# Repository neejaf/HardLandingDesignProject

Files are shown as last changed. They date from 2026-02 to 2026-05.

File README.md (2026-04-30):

# Hard Landing – Landing Gear Design Project

This repository contains all materials for the MEE 342 landing gear design project.

## Project Phases
- [Phase 1 – System Description and Kinematics](phase1.md)
- [Phase 2 – Detailed CAD Design and Engineering Analysis](phase2.md)
- [Phase 3 – Prototyping, Testing and Reflection](phase3.md)

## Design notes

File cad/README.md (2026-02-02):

# CAD

This directory contains CAD models and exported files for the landing gear design.

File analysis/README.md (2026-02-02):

# Analysis

This folder contains hand calculations, kinematic derivations, and summaries of simulation results.

Detailed analysis will be added in later phases.

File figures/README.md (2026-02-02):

# Figures

This folder contains sketches, diagrams, CAD screenshots, and images used in the project report.

Figures will be added as the design progresses.

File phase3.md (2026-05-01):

# Phase 3 – Prototyping, Testing & Reflection

## Fabrication Details

- Printer: Bambu Lab P1S  
- Material: PLA  
- Settings:  
  - Preset: 0.20 mm Standard (Bambu Studio)  
  - Supports: Tree supports  
- Scale:
  - Entire assembly scaled to 4.2% of original design  
  - Pins scaled further (ex: 60 mm → 50 mm → then scaled 4.2%)

- Reprints:
  - Wheels/Tires:
    - Originally hollow → poor print quality
    - Redesigned as solid → reprinted successfully

- Notes:
  - Supported regions had poor surface finish  
  - Small scale reduced print accuracy  

---

## Assembly Procedure

- Strut + torque link + pins printed as one piece  
- Bogie printed with pin pre-inserted (snap-fit into strut fork)  
- Wheels and tires printed together  
- Tires spray painted black  

---

## Assembly Challenges

- Tight tolerances did not scale well  
- Pins difficult to fit at small scale  
- Rough surfaces from supports affected fit  

---

## Testing Plan

- Checked:
  - Rotation of joints  
  - Fit between components  
  - General smoothness  

---

## Results

- Snap-fit worked for bogie connection  
- Rotation was functional but not perfectly smooth  
- Supported areas showed reduced quality  

---

## Comparison to Phase 2

- Expected:
  - Clean fits and smooth motion  
- Actual:
  - Tolerance issues and rough interfaces  
  - Reduced precision due to scaling  

---

## Failures & Mistakes

- Designed tolerances based on CAD, not printer capability  
- Scaling to 4.2% made tolerances too tight  
- Hollow wheel design failed → required redesign  
- Overuse of supports reduced surface quality  

### Link Failure (Retraction Link)

One of the critical failures occurred in the retraction link component (shown below).

<table>
  <tr>
    <td align="center">
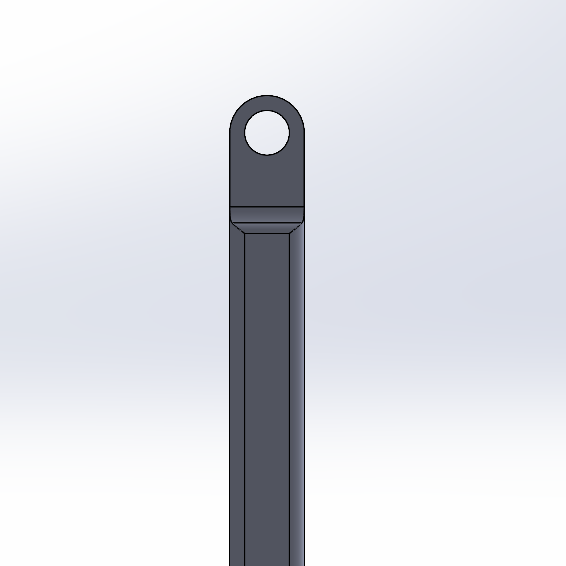
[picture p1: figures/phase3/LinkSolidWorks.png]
      <br>
      CAD Model
    </td>
    <td align="center">
      <br>
      Printed Part
    </td>
  </tr>
</table>

- In the CAD model, the hole regions had sufficient surrounding material for strength
- However, after scaling to 4.2% and printing in PLA:
  - The effective wall thickness around the holes was significantly reduced
  - Layer-based printing introduced weak points around the circular geometry
- This resulted in a stress concentration at the hole
- The part failed at this location during handling/assembly and required reprinting

Root Cause:
- Geometry was not adjusted for small-scale manufacturing
- Printer resolution limits reduced effective material thickness
- Layer adhesion + circular hole geometry weakened the region further

### Poor Surface Quality / Stringing (Strut Component)

<p align="center">
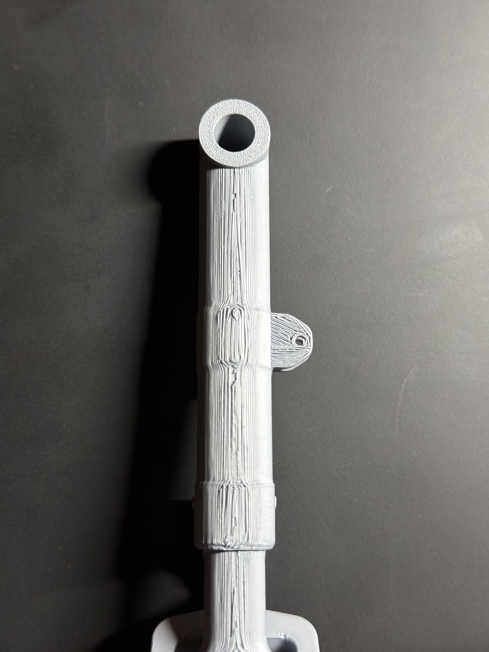
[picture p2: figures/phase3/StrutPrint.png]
  <br>
  Printed Strut (Surface Defects / Stringing)
</p>

The strut component exhibited noticeable surface defects and stringing, particularly along vertical faces.

- The print showed:
  - Stringing between features  
  - Uneven extrusion lines  
  - Rough surface finish  

- These defects were most prominent in:
  - Thin vertical sections  
  - Areas with frequent start/stop of extrusion  
  - Regions requiring support  

Root Cause:
- Small scale (4.2%) reduced feature resolution  
- Standard print settings were not optimized for fine features  
- Retraction and cooling were not ideal for this geometry  

Impact:
- Reduced surface quality  
- Potential reduction in strength  
- Poorer fit between components

## Improvements (Version 2)

- Increase tolerances for all mating parts  
- Reduce reliance on small pins  
- Design for fewer supports (better orientation)  
- Avoid hollow features at small scale  
- Consider larger scale or finer print settings  

---

## Key Takeaways from Design

- CAD tolerances ≠ printable tolerances  
- Scaling down amplifies manufacturing limitations  
- Supports negatively affect surface finish  

## Key Takeaways from Building

- Design for assembly tends to add extra complexity to model
- Proper engineering design process takes multiple physical models (as shown by our "Improvements" section)
- Orientation of 3D print greatly impacts strength of parts
- How to scale stress down from ANSYS to 3D model

<p align="center">
  <br>
  Final Model w/ Poster
</p>

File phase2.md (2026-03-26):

# Phase Two: Project Report  
Hard Landing – Landing Gear Project  

<p align="center">
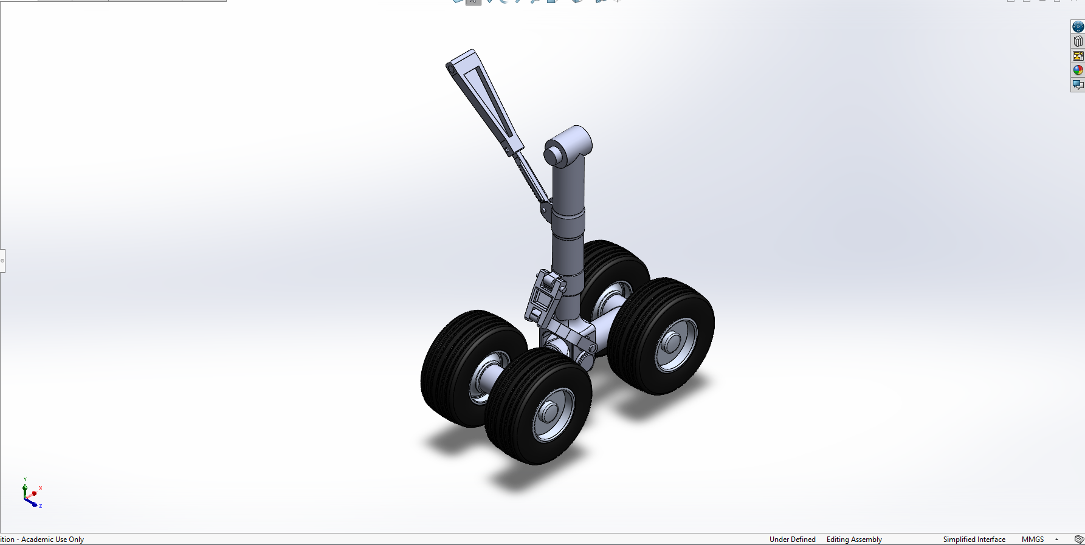
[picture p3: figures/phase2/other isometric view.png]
    </td>
  <p/>

<p align="center">
Aiden Beam, Jack Bessette, Ben Kolecki, Evan Morris, Nordin Jafar 
<p align="center">
Arizona State University
  </p>
<p align="center">
MEE 342  
  </p>

## **Final Design Overview**
This landing gear system is designed for a wide-body commercial aircraft operating under typical taxi, takeoff, landing, and flight conditions. During ground operation, the gear remains in its vertical, locked configuration to support the aircraft, and retracts during flight to reduce aerodynamic drag.

The design is based on a representative aircraft weight consisting of structural mass and payload. For loading assumptions, 90% of the total aircraft weight was taken to be supported by the main landing gear, with the remaining load carried by the nose gear. Since there are two main landing gear assemblies, each gear supports approximately 45% of the total aircraft weight under static conditions.

The system consists of three primary sections:
- **Main strut and wheel assembly**, which carries vertical landing and ground loads  
- **Bogie and fork interface**, which transfers forces from the wheels into the strut  
- **Two-bar linkage mechanism**, which controls retraction and deployment  

The design maintains a clear load path from the wheels through the bogie and into the main strut, ensuring forces are transferred efficiently through the structure.

Multiple loading conditions were considered:
- Landing loads
- Static loads  
- Braking loads  
- Stowed configuration

These cases capture both vertical and combined loading conditions seen in real operation.
Overall, the design focuses on realistic load distribution, efficient force transfer, and identifying critical stress regions.
<br>
<p align="center">
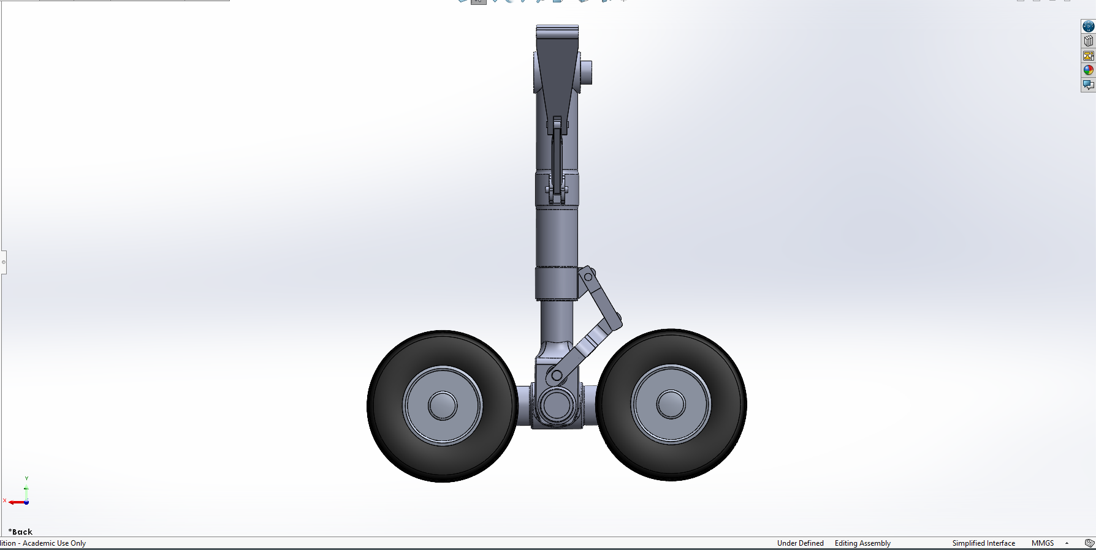
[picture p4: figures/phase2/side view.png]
	</td>
	<p/>

### **Landing gear deployment/retraction sequence**
<p align="center">
Isometric View
<br>
	
[watch the assembly video](https://github.com/user-attachments/assets/6c1ffd8b-b0af-4d7d-89b4-459098cd728c)

<br>
<p align="center">
Frontal View
<br>
	
[watch the assembly video](https://github.com/user-attachments/assets/f484d572-f8e7-468a-845d-adacea77aa67)

<br>

<p align="center">
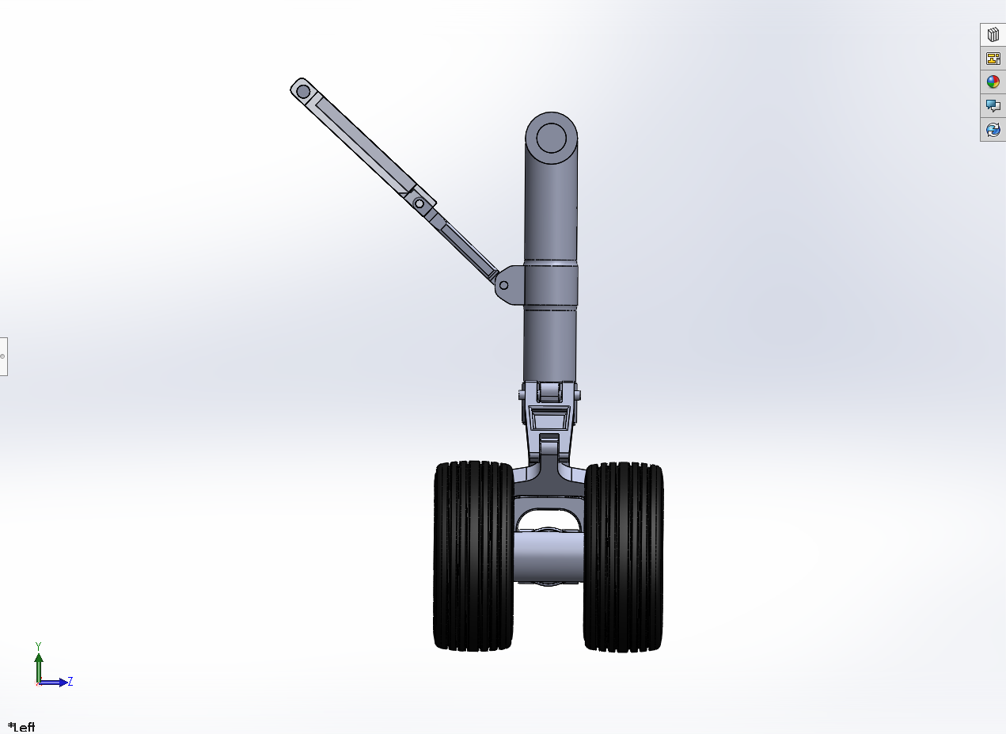
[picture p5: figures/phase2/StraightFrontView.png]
	</td>
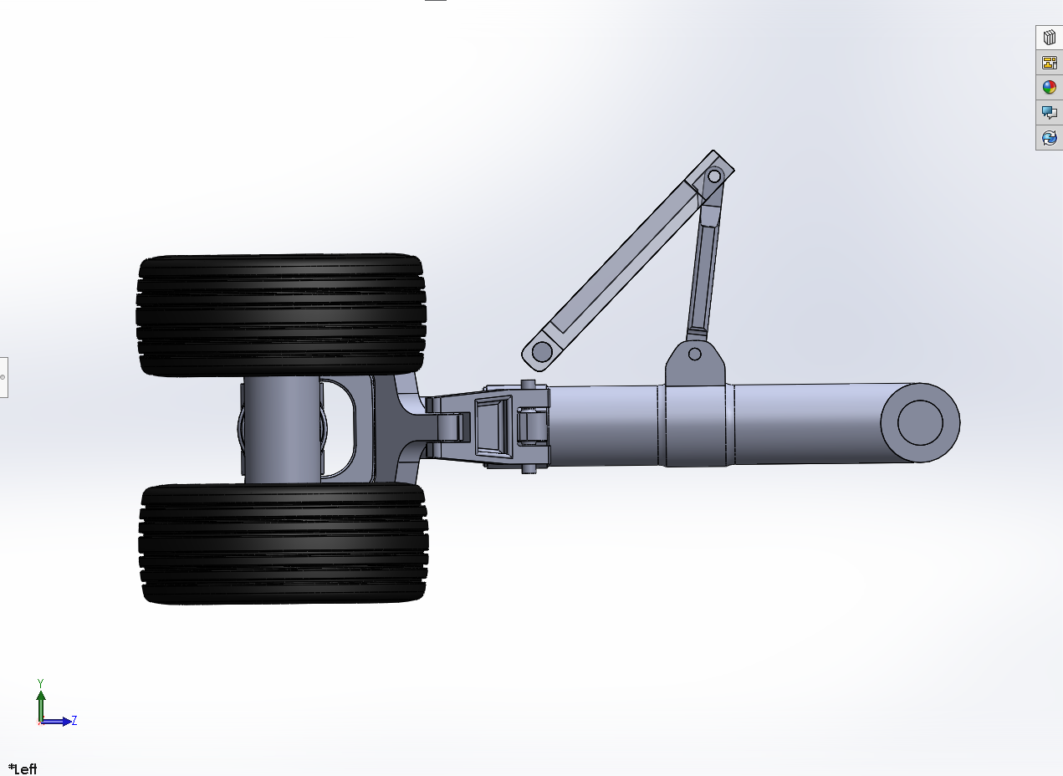
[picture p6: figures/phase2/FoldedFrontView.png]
	</td>
	
  <p align="center">
<br>

**Full 3D Assembly**
<p align="center">
	<p align="center">
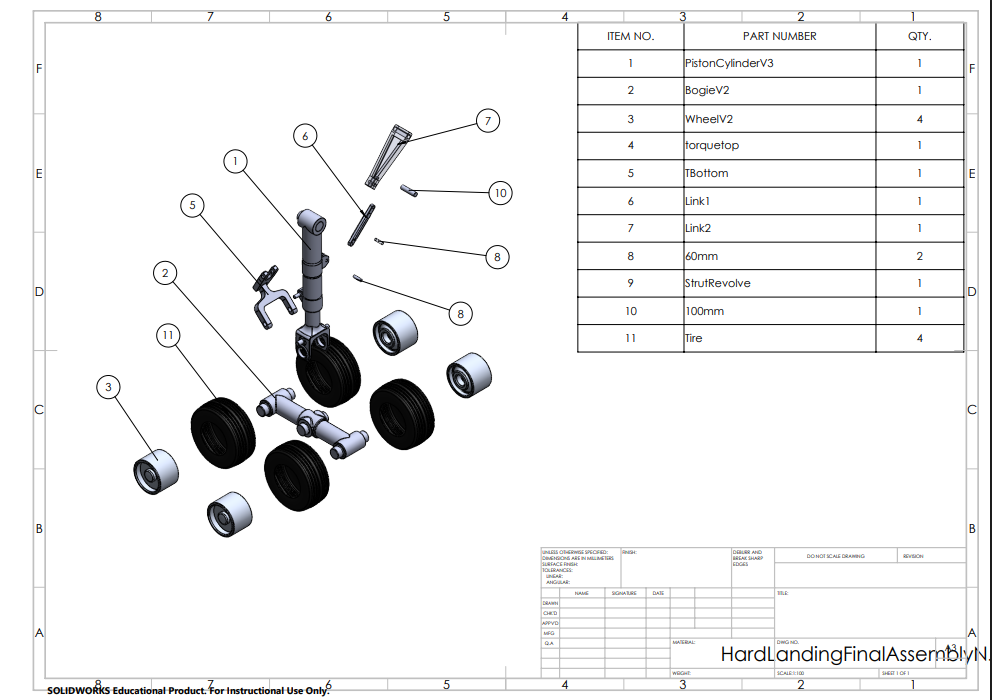
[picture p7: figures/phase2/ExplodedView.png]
  </td>
<p/>
	<p/>
	
<br>  

## Description of Major Design Decisions and Changes from Phase 1

### Increased wheel count to better match real configurations
- Added three additional wheels to more closely reflect typical commercial airliner landing gear
- Improves realism of load distribution in simulations
- Results in a more stable and balanced system under load
- Wheelbase was updated to accommodate the additional wheels

### Reinforced linkage-to-strut connection
- Strengthened the connection between the two-bar linkage and main strut
- Allows the assembly to handle higher loads
- Increases the overall factor of safety

### Pin relocation for improved kinematics
- Raised the pin supporting the two-bar linkage
- Allows full horizontal stowage of the strut
- Enables more realistic retraction within the fuselage
- Eliminates previous angled configuration that would place components outside the aircraft envelope

## **Discussion of Design for Assembly and Design for 3D Printing**
Phase 3, we plan to scale this model down to fit in a 256mm 3D print bed, made with PLA filament. Certain dimesnsions will be adjussted to account for 3D print tolerances to ensure intented kinematics is possible.

### Design for Assembly
- Assembly is kept simple using pin connections for all joints
- Parts are split into manageable components (strut, bogie, linkage, etc.)
- Small clearances are included to avoid binding during motion

### Design for 3D Printing
- All parts are sized to fit within the printer build volume
- Basic clearances are included to account for print tolerance
- Parts are oriented to reduce the need for supports where possible
- Design prioritizes functionality over strength since this is a demonstration model
<br>

## **Analysis**
- As mentioned before, four loading cases are evaulated: landing impact, static load, braking (rejected takeoff), and stowaway configuration. These cases represent the primary or critical conditions the landing gear is expected to experience.
- Loads are derived by assuming the main landing gear supports approximately 90% of the total aircraft weight, distributed equally between the two main gear assemblies. This approach follows standard landing gear design practices.
- For landing conditions, a load factor (n ≈ 2) is applied to account for impact during touchdown. Braking conditions introduce horizontal forces due to friction at the wheels, while the static case considers steady vertical loading. The stowed configuration evaluates the effect of gravity and constraints during retraction.
- For each case, forces and constraints are applied to approximate real-world conditions, and resulting stresses, deformations, and reaction forces are analyzed to evaluate structural performance and factor of safety.
<br>

### Landing (Tilted Oleo @ 9 degrees - 3.4MN Load)
- For the landing condition, a load factor of n ≈ 2 was applied to represent impact during touchdown. This resulted in an equivalent load of approximately 3.4 MN acting through the wheel assembly.
- The load was applied at the wheel contact locations, with constraints at the upper strut interface to approximate attachment to the aircraft structure. A tilted configuration (~9°) was used to reflect the expected geometry during initial ground contact.

**Von-Mises Equivalent Stress - 472.99 MPa**

 - The maximum von Mises stress of 472.99 MPa occurs near the lower strut-to-bogie interface, indicating this region experiences the highest combined bending and shear loading. This is consistent with expectations, as this joint transfers load from the wheels into the main structure.
<p align="center">
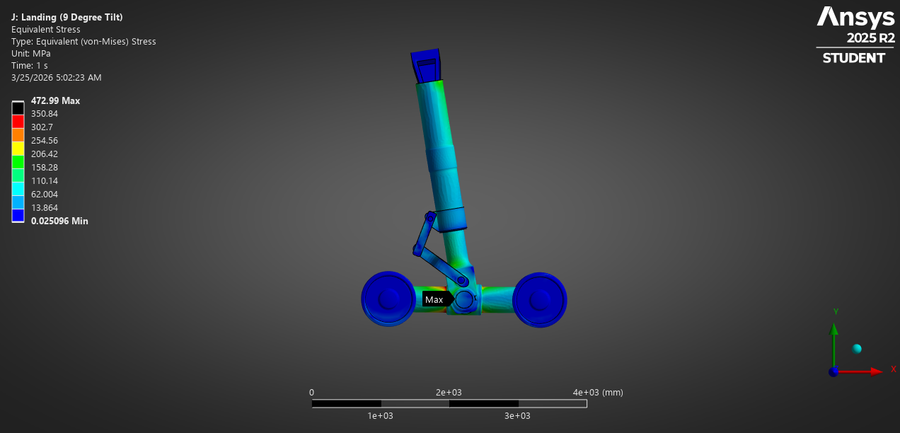
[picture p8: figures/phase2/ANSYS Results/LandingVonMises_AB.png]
  
</p>

**Stress Factor of Safety - 3.35**

 - The resulting factor of safety of 3.35 suggests that the structure is within acceptable limits under landing conditions, assuming the selected material properties. Deformation was primarily concentrated along the strut, with no excessive displacement observed that would indicate instability.
<p align="center">
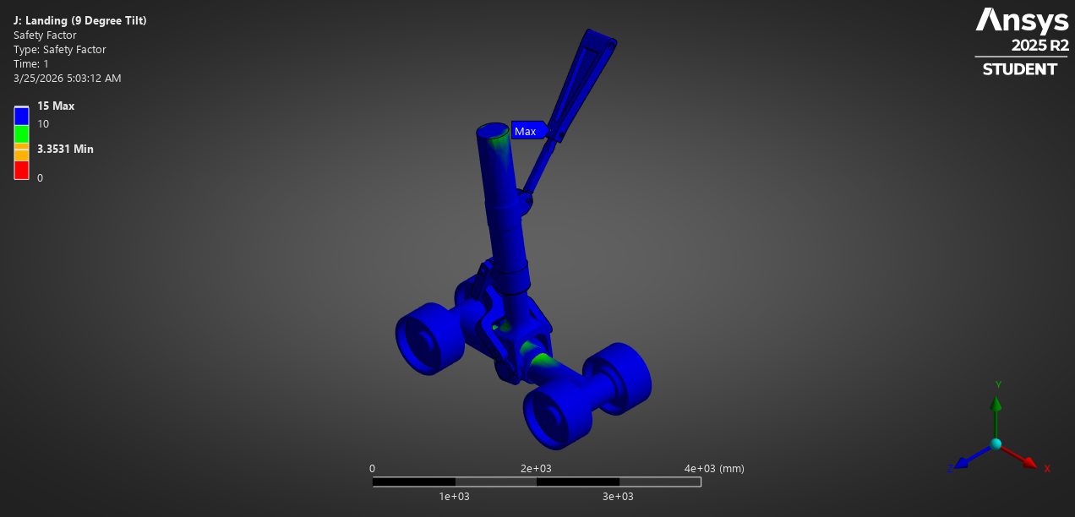
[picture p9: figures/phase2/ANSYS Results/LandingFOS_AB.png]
  
</p>

**Fatigue Analysis - Equivalent Alternating Stress - 269.5 MPa**
<p align="center">
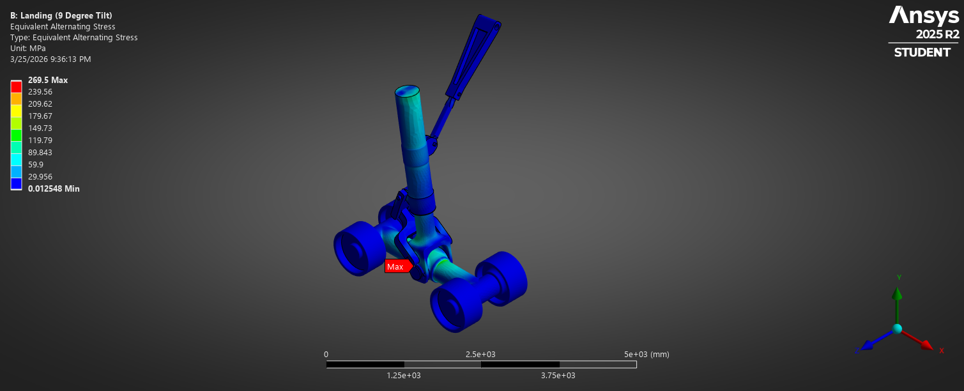
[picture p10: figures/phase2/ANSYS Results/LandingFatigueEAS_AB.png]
  
</p>

**Fatigue Analysis - Factor of Safety - 2.28**

<p align="center">
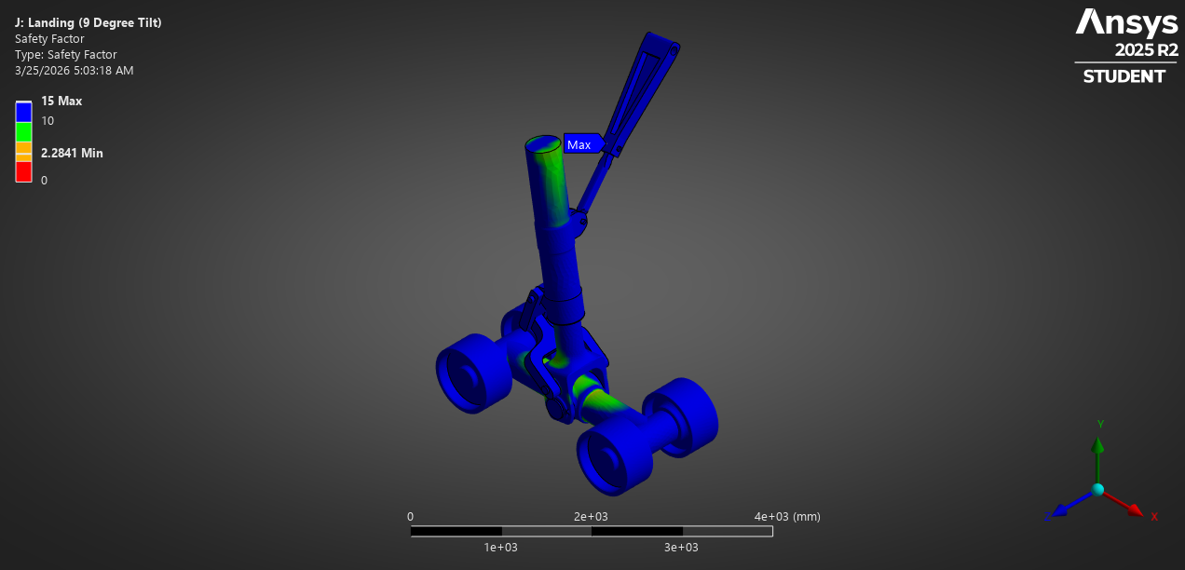
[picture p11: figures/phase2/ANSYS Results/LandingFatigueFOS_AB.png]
  
</p>

 - Fatigue results show an equivalent alternating stress of 269.5 MPa, with a corresponding fatigue factor of safety of 2.28. This indicates that, while safe for repeated loading, this region may be a critical location for long-term durability and should be monitored in future iterations.

### Static - "Standing" Load (1.8MN Vertical Load)
 - For the static condition, a vertical load of 1.8 MN was applied to represent the aircraft at rest. This load was distributed through the wheel assembly, with constraints applied at the upper strut interface to simulate attachment to the aircraft structure.

**Von-Mises Equivalent Stress - 220.81 MPa**

 - The maximum von Mises stress of 220.81 MPa occurs near the lower strut and bogie interface, consistent with the primary load path from the wheels into the main structure.
<p align="center">
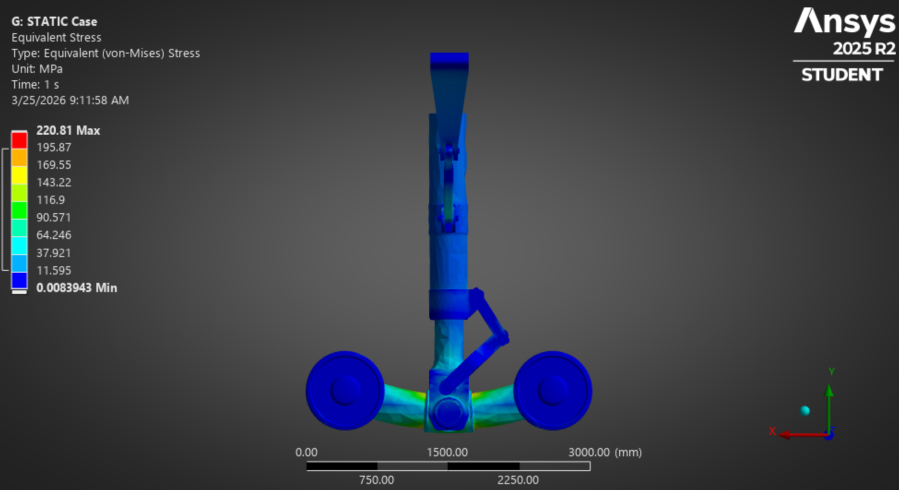
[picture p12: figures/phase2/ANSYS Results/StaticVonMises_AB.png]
  
</p>

**Stress Factor of Safety - 7.18**

 - The resulting factor of safety of 7.18 indicates the structure is well within safe limits under static conditions, suggesting the design is not governed by this loading case.
<p align="center">
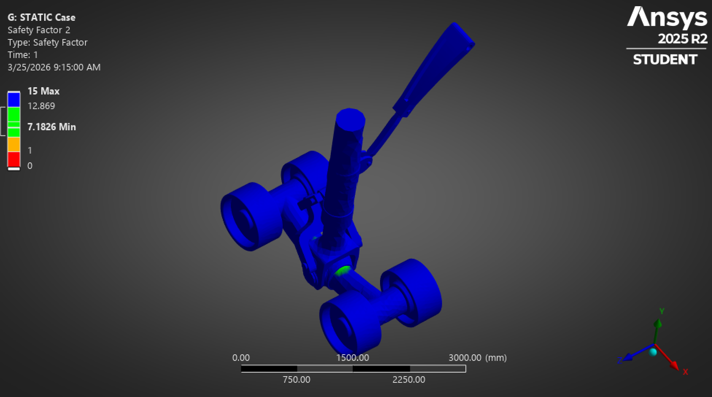
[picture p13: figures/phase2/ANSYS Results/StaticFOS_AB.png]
  
</p>

**Fatigue Analysis - Equivalent Alternating Stress - 117.1 MPa**

 - Fatigue results show an equivalent alternating stress of 117.1 MPa with a fatigue factor of safety of 4.89. This further confirms that the static condition is not critical for long-term durability.
<p align="center">
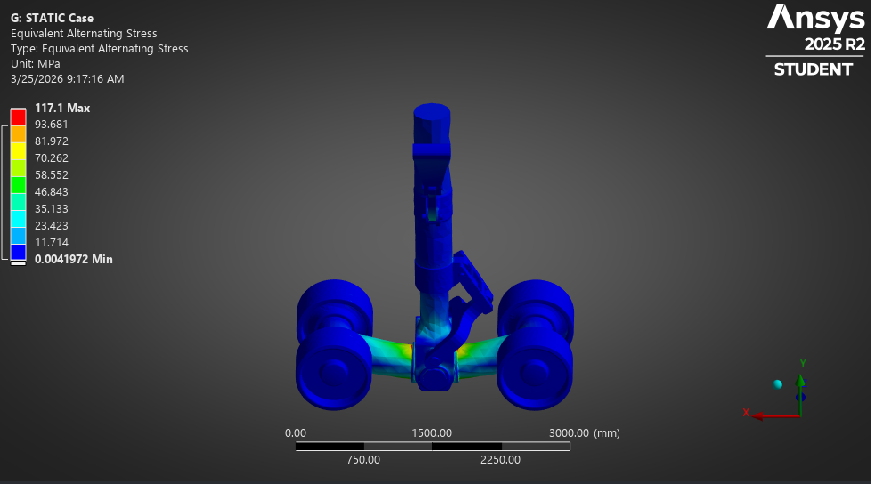
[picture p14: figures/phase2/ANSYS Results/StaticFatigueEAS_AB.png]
  
</p>
 
**Fatigue Analysis - Factor of Safety - 4.89**
<p align="center">
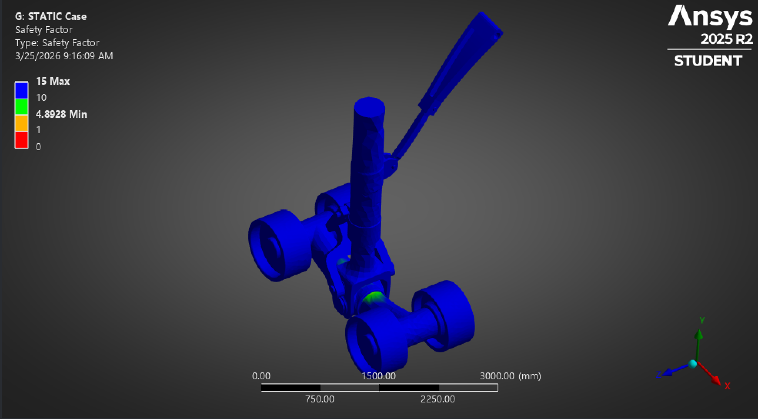
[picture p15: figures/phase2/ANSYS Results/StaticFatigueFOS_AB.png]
  
</p>

### Braking -  (1.8MN Vertical Load + 640KN Horizontal Load)
- For the braking condition, a vertical load of 1.8 MN was applied along with a horizontal load of 640 kN to represent friction forces during a rejected takeoff. The horizontal force was applied at the wheel contact locations, opposing motion, while constraints were applied at the upper strut interface to simulate attachment to the aircraft.

**Von-Mises Equivalent Stress - 538.11 MPa**
- The combined loading introduces significant bending in the main strut due to the moment created by the horizontal force acting at ground level. The maximum von Mises stress of 538.11 MPa occurs near the upper strut region, indicating this area is critical under combined loading.
<p align="center">
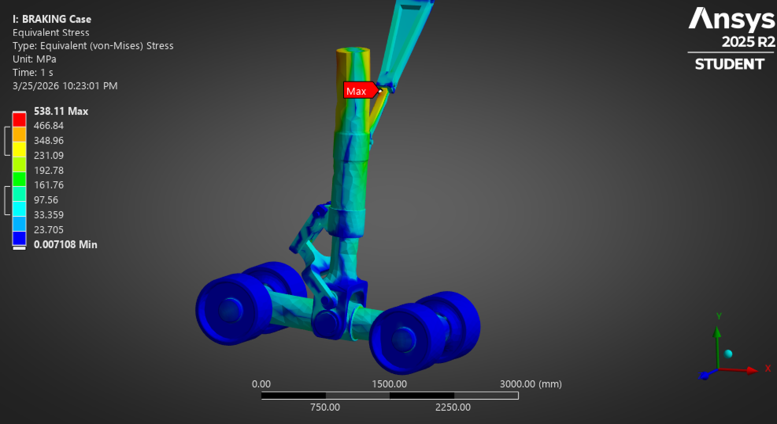
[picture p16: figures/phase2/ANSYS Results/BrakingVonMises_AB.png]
  
</p>

**Stress Factor of Safety - 2.94**
 - The resulting factor of safety of 2.94 is lower than both the static and landing cases, suggesting that braking is one of the more critical loading scenarios for the design.
<p align="center">
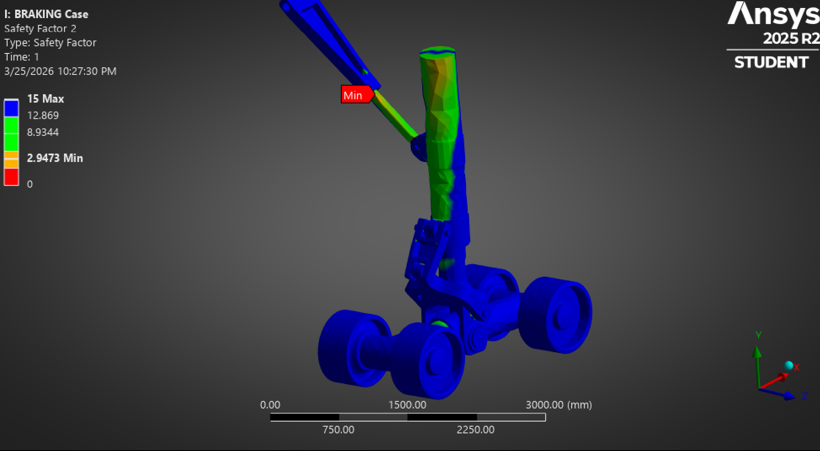
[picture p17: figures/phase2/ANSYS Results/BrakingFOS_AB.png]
  
</p>

**Fatigue Analysis - Equivalent Alternating Stress - 312.61 MPa**
 - Fatigue results show an equivalent alternating stress of 312.61 MPa with a fatigue factor of safety of 2.01. This indicates that repeated braking loads may be a limiting factor for long-term durability.
<p align="center">
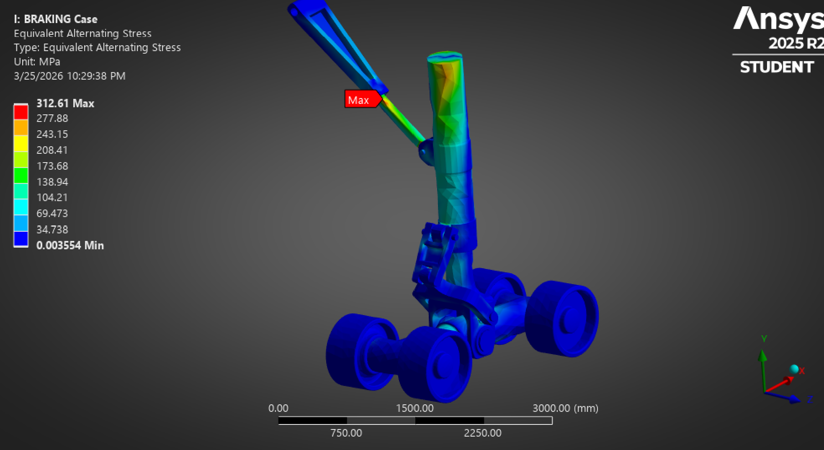
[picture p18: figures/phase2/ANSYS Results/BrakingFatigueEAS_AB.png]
  
</p>

**Fatigue Analysis - Factor of Safety - 2.01**
<p align="center">
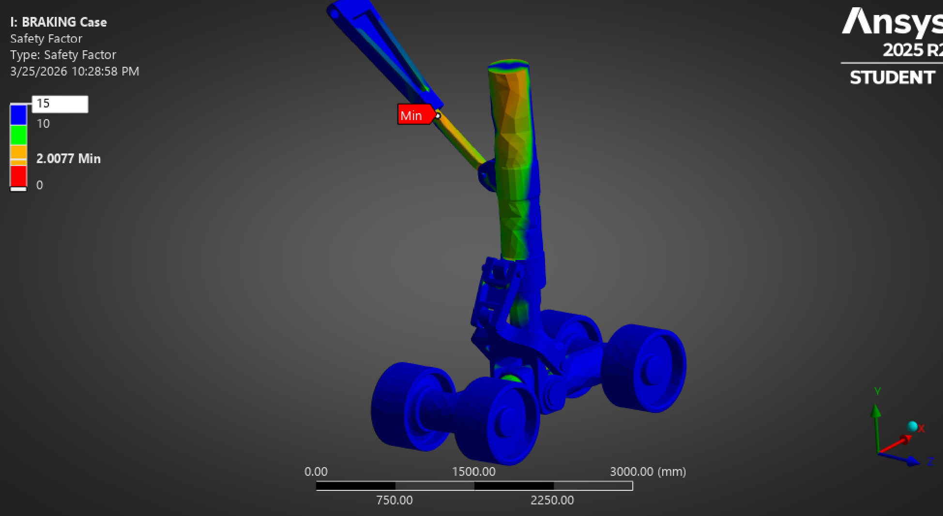
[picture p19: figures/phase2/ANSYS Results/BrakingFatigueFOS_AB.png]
  
</p>

### Retracted Configuration - (Applied Gravity)
- For the retracted configuration, gravity was applied to the assembly to represent the loading condition while stowed within the aircraft. Constraints were applied at the upper strut interface to simulate attachment to the airframe.

**Von-Mises Equivalent Stress - 157.48 MPa**
- The maximum von Mises stress of 157.48 MPa occurs near the linkage and strut interface, where the weight of the assembly is transferred through the support structure. This is expected, as the linkage carries the load while holding the gear in the retracted position.
<p align="center">
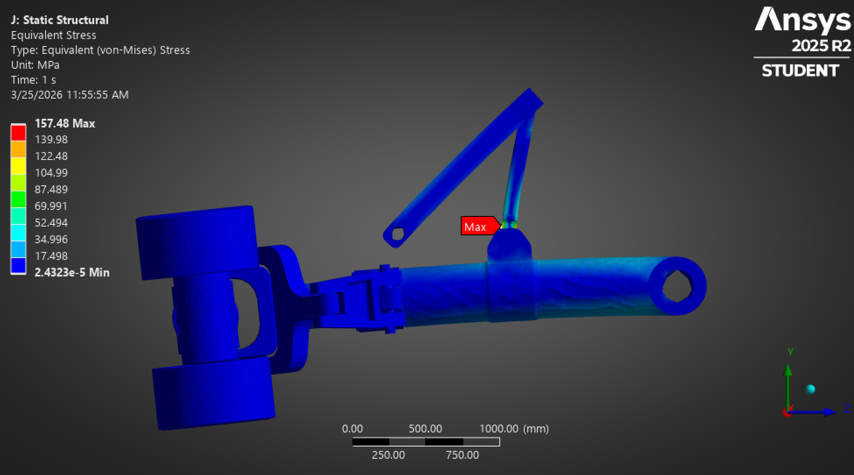
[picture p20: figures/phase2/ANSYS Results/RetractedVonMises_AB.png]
  
</p>

**Stress Factor of Safety - 10.07**
 - The resulting factor of safety of 10.07 indicates that the structure is well within safe limits under this condition. Stresses are relatively low compared to landing and braking cases due to the absence of external impact or horizontal forces.
<p align="center">
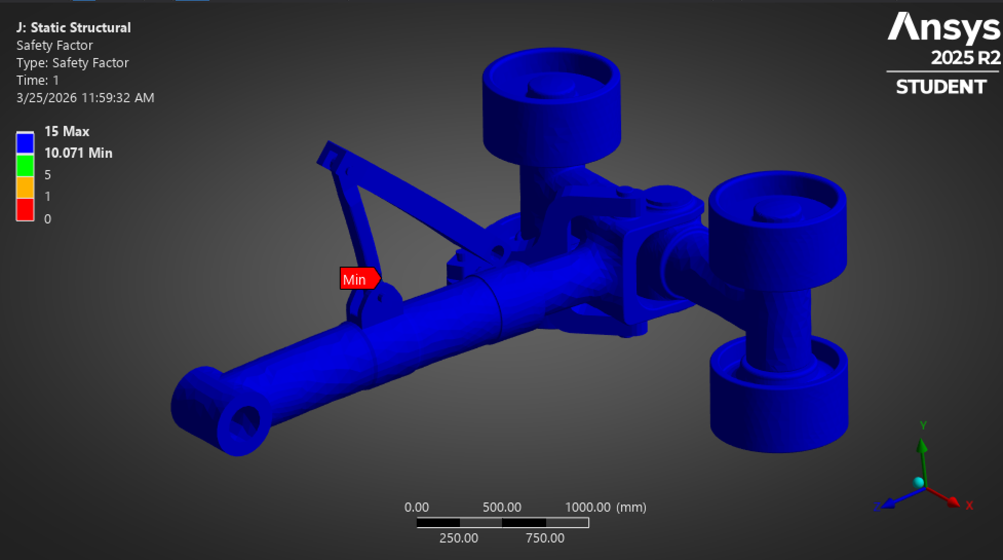
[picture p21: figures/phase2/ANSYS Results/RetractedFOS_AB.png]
  
</p>

**Fatigue Analysis - Equivalent Alternating Stress - 82.09 MPa**
 - Fatigue results show an equivalent alternating stress of 82.09 MPa with a fatigue factor of safety of 6.86, indicating that repeated cycling between deployed and stowed positions is not a limiting factor for the design.
<p align="center">
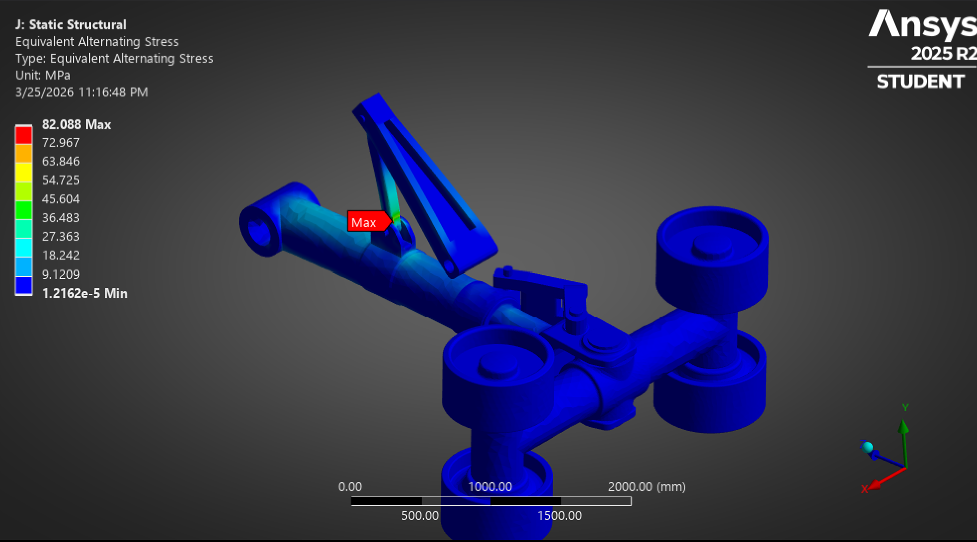
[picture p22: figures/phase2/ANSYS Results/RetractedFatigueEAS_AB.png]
  
</p>

**Fatigue Analysis - Factor of Safety - 6.86**
<p align="center">
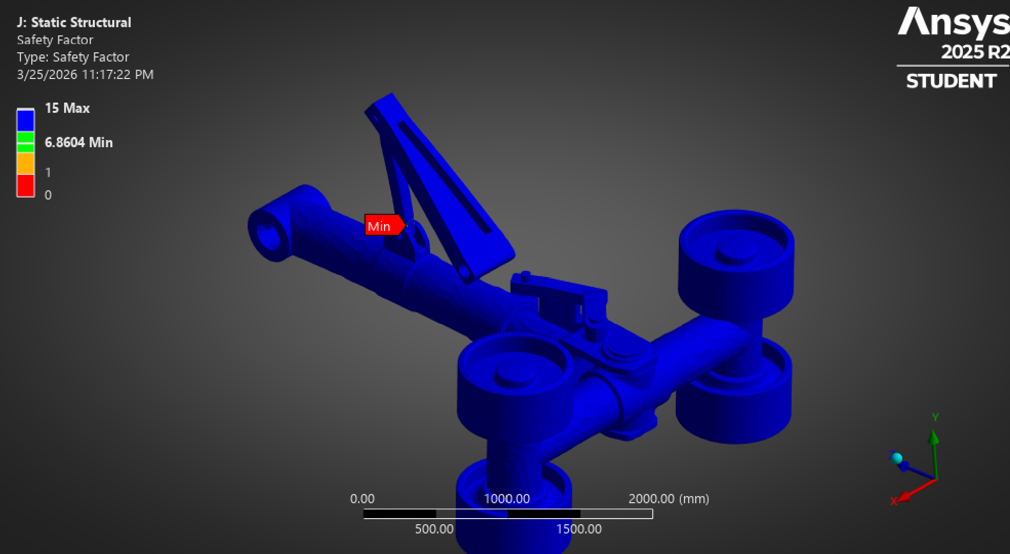
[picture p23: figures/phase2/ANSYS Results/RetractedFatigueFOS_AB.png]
  
</p>
- Overall, the retracted configuration is not a governing load case, but it verifies that the assembly can safely support itself while stowed.

## Material Properties and Fatigue Data

The structural components of the landing gear were modeled using 300M steel, an ultra-high-strength low-alloy steel commonly used in aerospace applications. 300M is a modified version of AISI 4340 steel, with added silicon and vanadium to improve hardenability, fatigue strength, and fracture toughness.

Material properties were defined in ANSYS using isotropic elasticity, with a Young’s modulus of 205 GPa, Poisson’s ratio of 0.28, and a density of 7850 kg/m³. A tensile yield strength of 1586 MPa and ultimate tensile strength of 1931 MPa were used for stress and factor of safety calculations.

Fatigue behavior was incorporated using an S–N curve representative of 300M steel. This data was based on published experimental results for smooth specimens under fully reversed loading conditions, providing a realistic basis for fatigue life estimation in the landing gear components.

## Loading Context and Modeling Assumptions

The applied static load per main landing gear was 1.8 MN. Assuming each main gear supports approximately 45% of the total aircraft weight:

Total Weight = 1.8 MN / 0.45 = 4.0 MN

Converting total weight to mass:

m = W / g = (4.0 × 10^6 N) / (9.81 m/s²) ≈ 4.08 × 10^5 kg

This corresponds to an approximate aircraft mass of **408,000 kg**, which is consistent with a wide-body commercial aircraft.

Landing loads of approximately 3.4 MN were derived using a load factor (n ≈ 2) to represent impact forces during touchdown. Braking loads include horizontal forces estimated using a friction coefficient consistent with dry runway conditions.

The oleo strut was modeled as a rigid structural member rather than a dynamic energy-absorbing system. In real landing gear, the oleo provides damping and reduces impact forces through hydraulic compression. This simplification allows for direct evaluation of structural stresses, but does not capture energy absorption effects, meaning landing stresses may represent a conservative estimate.

## **CAD Drawings - Critical Components and Exploded View**
 - The oleo and bogie were selected as critical components due to their role in transferring loads from the wheels into the main structure and consistently experiencing the highest stresses across multiple loading cases. These components are also key interface regions within the assembly, where forces are transmitted through pins and joints, making them critical for both structural integrity and overall system performance.
 - Interface stresses at pin connections were considered qualitatively, as these regions transfer load between major components. The results indicate that these areas coincide with regions of maximum stress observed in simulation, confirming their importance in the load path. Future iterations may include detailed bearing and shear stress calculations at these interfaces.

<table align="center">
  <tr>
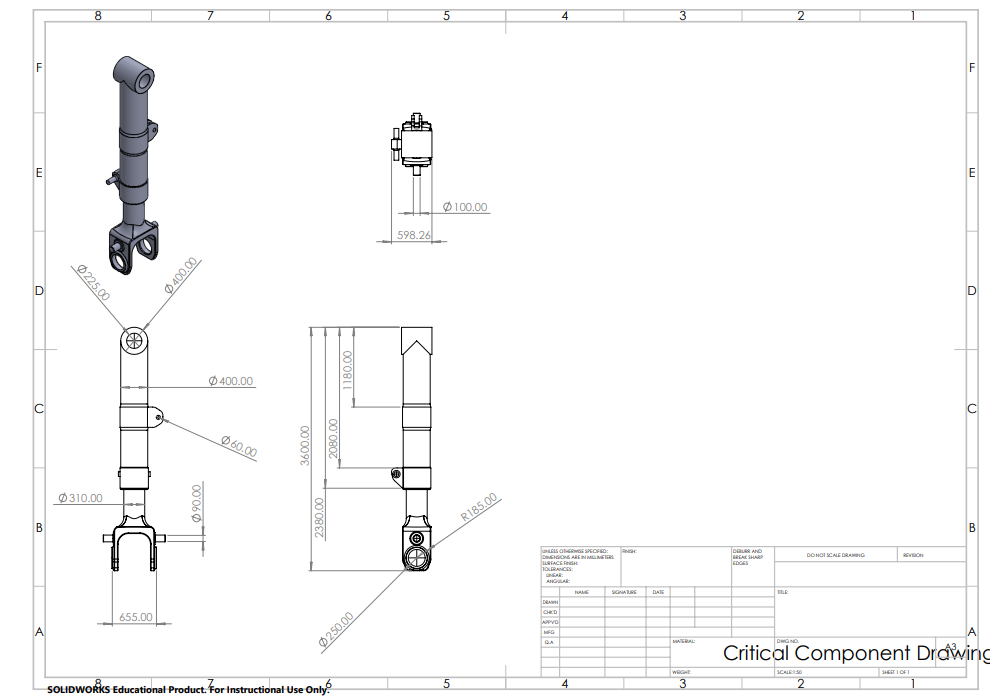
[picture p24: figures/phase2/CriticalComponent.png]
    <td></td>
	<td></td>
    <td></td>
  </tr>
  <tr>
	<td align="center"><em>Oleo</em></td>
	<td align="center"><em>Bogie</em></td>
    <td align="center"><em>Exploded View</em></td>
  </tr>
  </table>

## Global Safety Summary

Across all loading conditions, the braking case produced the highest stress and lowest factor of safety, making it the governing design condition. The landing case also resulted in significant stresses, particularly at the strut-to-bogie interface. Static and stowed configurations showed significantly lower stress levels and are not critical for design.

All cases resulted in factors of safety greater than 2, indicating acceptable structural performance. Fatigue analysis shows that braking loads may be the limiting factor for long-term durability, particularly at key interface regions.

## References

Currey, N. S. (1988). *Aircraft Landing Gear Design: Principles and Practices*. American Institute of Aeronautics and Astronautics.

The S–N curve used for fatigue analysis was referenced from published experimental data:

“Numerical Prediction of Fatigue Life for Landing Gear Considering the Shock Absorber Travel.” ResearchGate.

https://www.researchgate.net/figure/Test-S-N-curve-of-300M-steel-smooth-bar-specimen-Kt-1-R-1-f-110-Hz-a-testing_fig12_387991291.

Reference for material props: AZoM. 

(2013, July 11). AISI 300M Alloy Steel (UNS K44220).

https://www.azom.com/article.aspx?ArticleID=6671

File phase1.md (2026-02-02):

# Phase One: Project Report  
Hard Landing – Landing Gear Project  

<p align="center">
  System sketch
</p>

Aiden Beam, Jack Bessette, Ben Kolecki, Hunter Sam, Evan Morris, Nordin Jafar  
Arizona State University  
MAE 342  

## Executive Summary

 This project aims to design and 3D print a retractable and deployable rigid-strut landing gear, intended for kinematic evaluation and preliminary structural and failure analysis. The design implicitly represents a wide-body commercial aircraft main landing gear.
Some simplifications to note are that the design replaces hydraulic actuation with a motor-powered linkage mechanism that supports and deploys the rigid strut. This allows the team to focus on the mechanical motion of the system and how loads are carried through the structure. The landing gear is analyzed at full scale using hand calculations and simulation tools such as ANSYS to evaluate stresses, motion, and potential failure modes under realistic loads.

## System Function and Decomposition
**Primary Function**

The primary function of this landing gear is to provide rigid structural support for an aircraft during all ground operations. This includes taxiing, takeoff, and landings of all intensities. When deployed, the main rigid strut, or oleo, and wheel assembly are designed to absorb and redirect the loadings from landing into the airframe. The rigid design was selected so the Hard Landing team may prioritize understanding the mechanical motion and loading paths through a landing gear. Moreover, this allows the team to ensure the gear maintains its integrity while simulating realistic aircraft loading conditions in the aerospace industry.   

In addition to the structural support the structure must provide, landing gear must reliably retract and deploy over repeated cycles. When the aircraft is airborne, a motor will rotate and fold the landing gear assembly into the wheel well housing, all under a single degree of freedom. A single degree of freedom ensures a smooth retracting and deploying transition along a repeated kinematic path. The overall result of a retracting landing gear allows the assembly to reduce aerodynamic drag to optimize fuel efficiency and overall flight performance. 

<p align="center">
  System sketch
</p>
<table>
  <tr>
    <td align="center">
      CAD model
    </td>
    <td align="center">
      Hand sketch
     </td>
  </tr>
</table>

**Decomposition**

The landing gear system is composed of a small number of rigid components connected by pin joints to allow rotation during deployment and retraction (see scaled figure).
Sketch dimensions are intended for prototype demonstration. Primary components (as shown in figure)

**Wheel Leg / Oleo**  
Main rigid strut of the landing gear. Carries the wheel assembly and primary loads  

**Long Bar**  
Part of the linkage mechanism. Controls the motion of the wheel leg during retraction and deployment.

**Short Bar**  
Works with the long bar to guide the rotation path. Helps constrain the mechanism motion.

**Clamp**  
Connects the linkage to the wheel leg. Transfers motion and loads between the linkage and main strut  

Note - Pin joints are assumed at all rotating connections but are not shown in detail. Wheels and small hardware are omitted for clarity. The simplified component layout allows the mechanism motion and load paths to be analyzed without unnecessary complexity.

## Kinematics
<p align="center">
  System sketch
</p>

**Description**
-The landing gear mechanism is a planar linkage system composed of rigid members connected by pin joints. Based on the linkage layout, the system has one degree of freedom (1 DOF), meaning the entire motion is governed by a single input. Detailed kinematic derivations are provided in scanned notebook form
(click figures to expand)

<p align="center">
  <a href="figures/phase1/hunterkinematicspg1.jpg">
    
  </a>
  &nbsp;&nbsp;&nbsp;
  <a href="figures/phase1/hunterkinematicspg2.jpg">
    
  </a>
</p>

## Preliminary Failure Mode Review

**Static overload (primarily in the main leg)**  
-Design aims to incorporate a factor of safety high enough to not fail under typical or atypical loading.

**Fatigue / cyclic loading (bearings, smaller beams)**
-Repeated extension and retraction causes wear on bearings and other load-bearing joints.  
Design aims to use materials and designs capable of handling repeated loading and to prescribe routine maintenance.

**Misalignment**  
-Tires contacting the ground at angles other than vertical may cause uneven loading.  
Design aims to incorporate components that lock the system in fully extended or retracted positions.

**Temperature-based failure**  
-In warmer environments, elevated temperatures could result in deformation or material degradation.

## Analysis Methods

**Beam Theory**  
A primary study of the lending gear can be performed through beam analysis. The main strut, or oleo, can be treated as a beam and the supporting strut can be trivialized to a two force member. The team can study the strut under combined axial and bending loads to determine the locations of maximum bending and shear stress from loadings during landing. This simplified model is limited by its inability to account for the dynamic interaction between the two legs of the supporting strut as well as the pins in the structure. Ultimately, beam theory best serves as a primary validation tool for the primary strut of the landing gear. 

**ANSYS / Simulation Analysis**  
After creating individual parts and an assembly in SOLIDWORKS, the design can be imported to ANSYS so real world loadings can be applied to the housing and our structure. We will then analyze the beam under loading conditions that model what would be seen in the real world. ANSYS will help us identify and evaluate the failure modes of our system. Allowing us to make design improvements to our prototype and understand the impact of elements such as hydraulics in the industry 

## Critical Design Parameters
The success of the “Hard Landing” gear structure relies on the implementation of various critical design parameters. These parameters correspond to the structural integrity of the landing gear under load and ensure the mechanism operates as the kinematic relationships describe. 

**Pin to Clamp Length, ℓCD**

-The length front the pin at the top of the strut to the clamp, ℓ, is a critical parameter that directly impacts the angles that the supporting linkage bars must reach. Additionally, the location of the clamp along the oleo will determine the amount of torque the motor needs to rotate the free end with the wheel. 

**Motor Torque and Rotation Requirements**

-The hydraulics in the inspiration for “Hard Landing” have been replaced with rigid supports and rotation powered by a motor. The required torque of the stepper motor, along with the angle it must rotate to, must be calculated to bring the oleo to a 90 degree angle with the landing surface.

**Factor of Safety**

-A reasonably high factor of safety must be established after determining the highest stress components to avoid static overload and failure due to large loadings upon landing. 

**Supporting Strut Lockout**

-When the landing gear is deployed the angle between the short and long bar must be straight at 180 degrees. If this linkage is not at a straight angle, it will not effectively support the loading on the landing gear. The lengths of these bars and the pin at their linkage must be optimized to ensure they do not collapse under loading during landing.

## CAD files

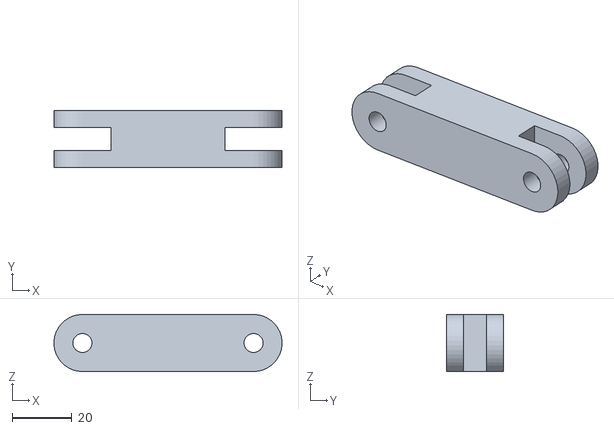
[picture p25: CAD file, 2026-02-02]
cad/simplecadphase1/ShortProto.STL
76.1 x 19.1 x 19.1

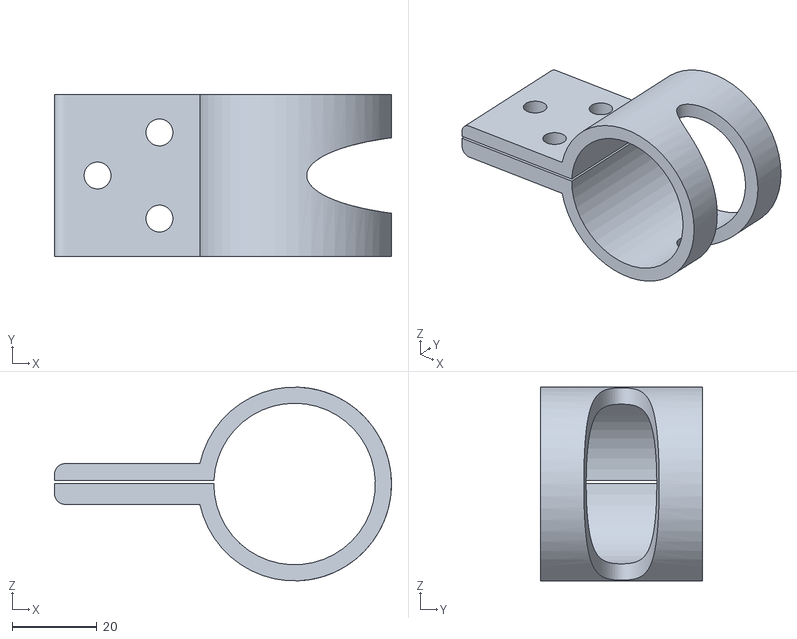
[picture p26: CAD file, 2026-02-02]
cad/simplecadphase1/CClamp.STL
79.5 x 38.1 x 45.7

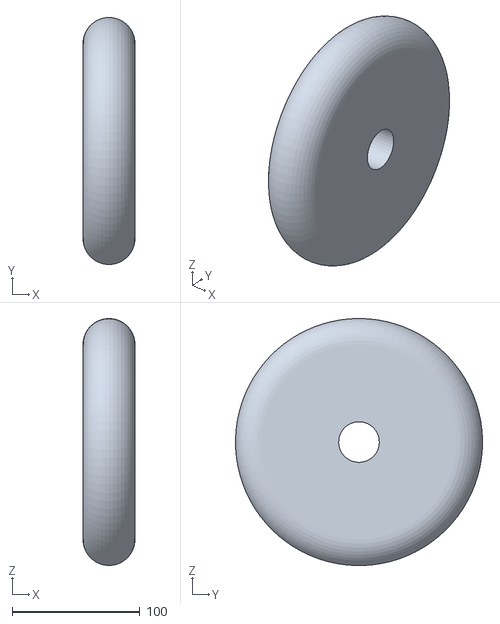
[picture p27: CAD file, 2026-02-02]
cad/simplecadphase1/WheelProto.STL
40.6 x 193.0 x 193.0

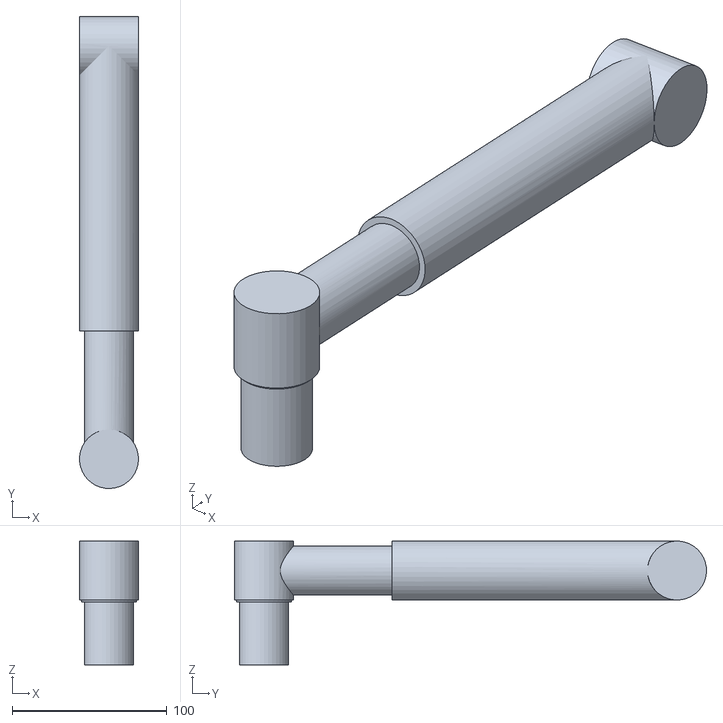
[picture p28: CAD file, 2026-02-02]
cad/simplecadphase1/WheelLeg.STL
38.1 x 304.8 x 80.0

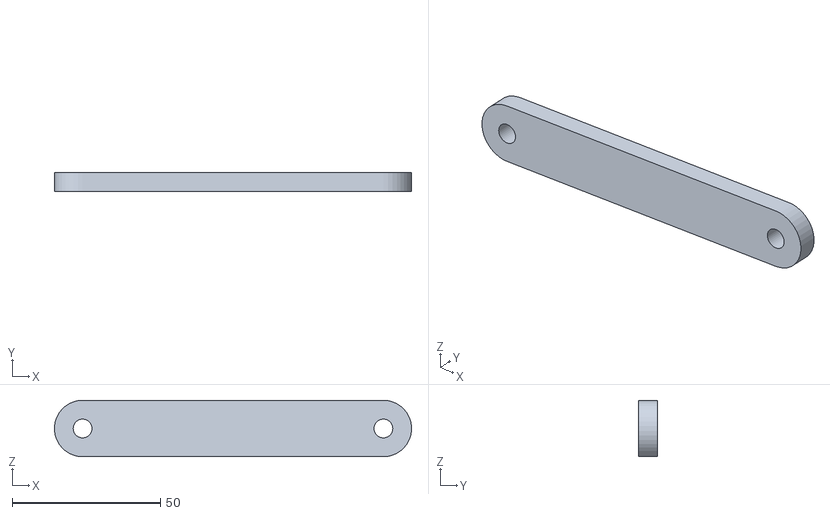
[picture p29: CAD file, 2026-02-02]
cad/simplecadphase1/LongProto.STL
120.6 x 6.35 x 19.1

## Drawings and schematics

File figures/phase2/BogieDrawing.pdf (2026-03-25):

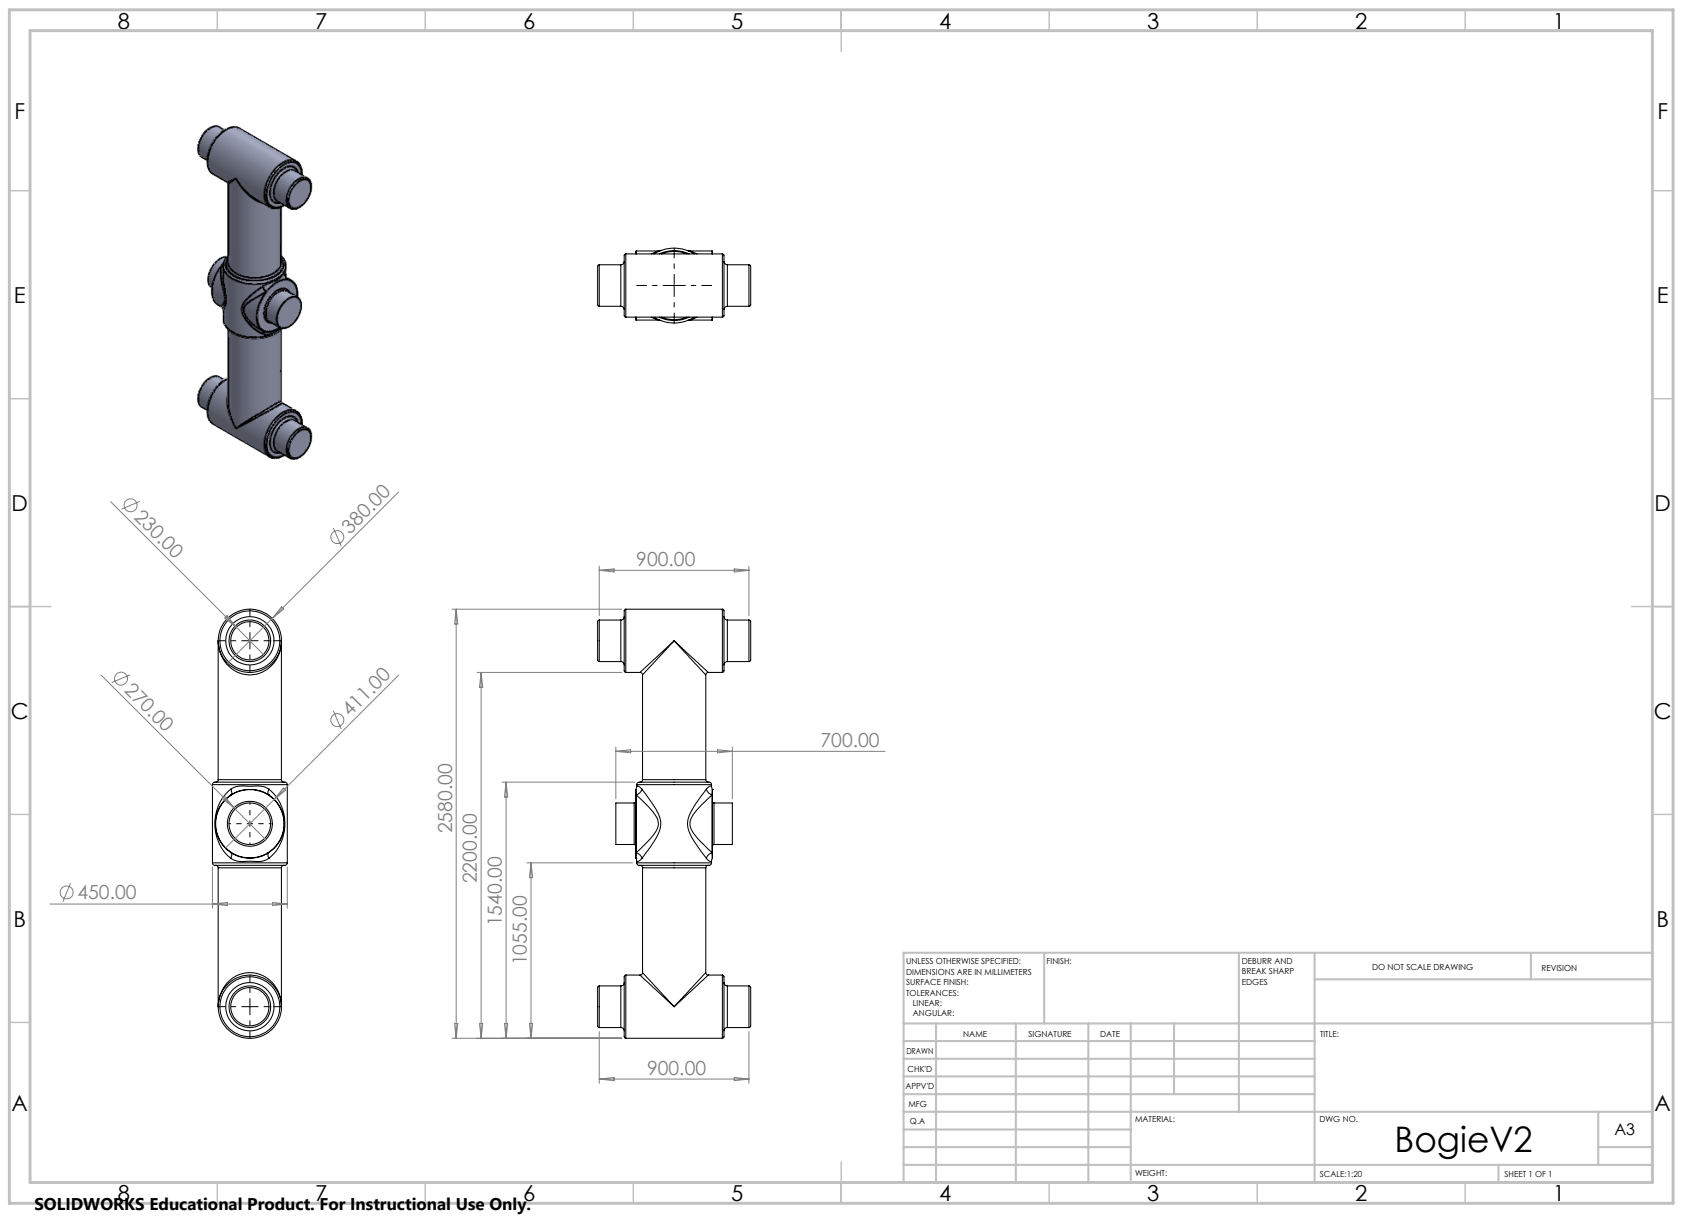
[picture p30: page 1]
FINISH:; DEBURR AND; BREAK SHARP; DO NOT SCALE DRAWING; REVISION; SCALE:1:20; SHEET 1 OF 1

UNLESS OTHERWISE SPECIFIED:
DIMENSIONS ARE IN MILLIMETERS
SURFACE FINISH:
TOLERANCES:
LINEAR:
ANGULAR:

NAME | SIGNATURE | DATE | | | | TITLE:

DRAWN
CHK'D
APPV'D
MFG
Q.A | | | | MATERIAL: | DWG NO. BogieV2 | A3

SOLIDWORKS Educational Product. For Instructional Use Only.

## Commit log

2026-02-02 Add project report for Hard Landing landing gear
    This document outlines the project report for the Hard Landing landing gear project, detailing the design, system functions, kinematics, failure modes, and analysis methods.
2026-02-02 Enhance phase1.md with project summary and functions
    Added an executive summary and clarified the primary function of the landing gear system.
2026-02-02 additional figures
    Added CAD and hand-drawn sketches to the Kinematics section.
2026-02-02 editts
    Removed figure captions for CAD and hand sketches.
2026-02-02 Insert table with CAD and hand sketches
    Added table with CAD model and hand sketch images for better visualization of the landing gear system.
2026-02-02 Enhance phase1.md with images for clarity
    Added images to the landing gear mechanism description.
2026-02-02 Enhance description and figure references in phase1.md
    Expanded description of the landing gear mechanism and added links to figures.
2026-02-02 Add README for CAD files directory
2026-02-02 Add README for Phase 1 CAD files
2026-02-02 Revise landing gear primary function description
    Expanded the description of the landing gear's primary function, detailing its structural support role and the mechanics of retraction and deployment.
2026-02-02 Revise analysis methods section in phase1.md
    Removed a line about temperature effects on material degradation in the analysis methods section.
2026-03-25 Enhance final design overview of landing gear system
    Expanded the final design overview of the landing gear system, detailing its operation, loading assumptions, and structural components.
2026-03-25 Simplify motor description in phase2.md
    Removed redundant explanation about motor functionality.
2026-03-26 Revise design decisions section for clarity and detail
    Updated section headers and improved clarity of design decisions. Enhanced descriptions for changes made from Phase 1, focusing on wheel count, linkage strength, and pin relocation.
2026-03-26 Expand design discussion for assembly and 3D printing
    Added sections for Design for Assembly and Design for 3D Printing, outlining assembly simplicity and 3D printing considerations.
2026-03-26 Revise analysis section and add landing conditions heading
    Corrected spelling errors and improved clarity in the analysis section. Added a new heading for the landing conditions.
2026-03-26 Update Landing section with new Von-Mises results image
    Removed old equivalent stress images and added a new image for Landing Von-Mises results.
2026-03-26 Add references section to phase2.md
    Added references section with a citation for aircraft landing gear design.
2026-03-26 Update phase2.md with additional references
    Added references for fatigue analysis and material properties.
2026-04-27 Document Phase 3 prototyping and testing results
    Added detailed sections on fabrication, assembly, testing, and improvements for Phase 3.
